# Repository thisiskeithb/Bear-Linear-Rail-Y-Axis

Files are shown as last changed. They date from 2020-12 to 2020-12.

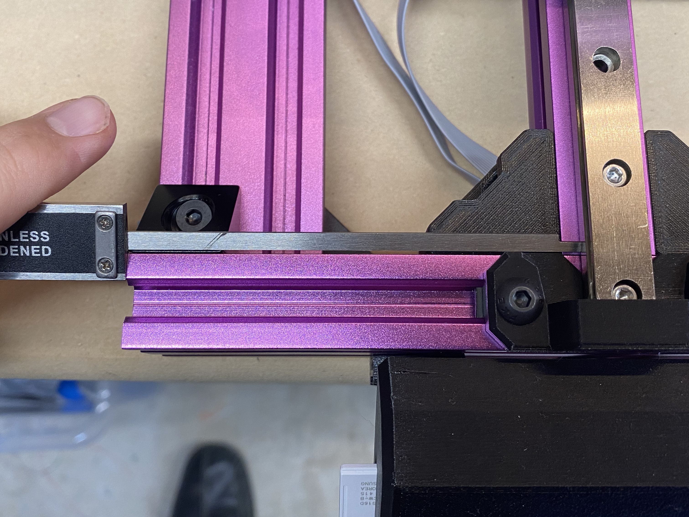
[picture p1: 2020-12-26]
img/left_rail_distance_2.jpg

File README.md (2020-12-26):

# Prusa MK3S Bear Y-Axis Linear Rail Upgrade

<p align="center">
  
</p>

## This guide is a work in progress
It is incomplete and subject to change. Use at your own risk.

## ⚠️ CAUTION! ⚠️

Before you begin, make sure you are using [MK3S Bear Upgrade V2.0](https://github.com/gregsaun/prusa_i3_bear_upgrade) or newer because the Y-axis uses the belt holder under the carriage to bump into the Y-axis motor holder. Without this upgrade, it will not pass Prusa's Self Test.

If you're using the [SKR Bear firmware](https://github.com/codiac2600/SKR-Bear-Marlin) this won't be an issue.

## Bill of Materials

| QTY | Length | Description | Source |
| :-: | :----: | :--- | :--- |
| 2 | 370mm  | MGN12 linear rail **\*** | |
| 3 | | MGN12H carriage block **\*** | |
| 2 | 331mm  | 2020 V-slot extrusion | |
| 18  | 8mm | M3 button head or cap head screw | [Amazon](https://amzn.com/B07B8FBT46/) / [OpenBuilds](https://openbuildspartstore.com/button-head-screws-m3-25-pack/) / [McMaster-Carr](https://www.mcmaster.com/91239A113) / [AliExpress](https://www.aliexpress.com/item/4000038065691.html) |
| 6 | 6mm | M3 flat head screw | [McMaster-Carr](https://www.mcmaster.com/91294A126) / [AliExpress](https://www.aliexpress.com/item/33049019185.html) |
| 18  | | M3 t-nuts | [Amazon](https://amzn.com/B07SDFCTD4/) / [OpenBuilds](https://openbuildspartstore.com/tee-nuts-m3-10-pack/) / [AliExpress](https://www.aliexpress.com/item/32825357262.html) |
| 20  | 8mm | M5 screws | [Amazon](https://amzn.com/B07B2RV4K6/) / [OpenBuilds](https://openbuildspartstore.com/low-profile-screws-m5-10-pack/) / [McMaster-Carr](https://www.mcmaster.com/91239A222) / [AliExpress](https://www.aliexpress.com/item/4000038065691.html) |
| 20  | | M5 t-nuts | [Amazon](https://amzn.com/B01HKMF2EE/) / [OpenBuilds](https://openbuildspartstore.com/tee-nuts-m5-10-pack/) / [AliExpress](https://www.aliexpress.com/item/32965780205.html) |

**\*** _If you are located in the USA, 2x 370mm MGN12 linear rails with dual carriage blocks from [Printed Solid](https://www.printedsolid.com/products/ldo-linear-rail-mgn12h-with-one-carriage-in-300-400-500-700mm-lengths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) will work. You will have one spare carriage block._

### Optional Bill of Materials
| QTY | Description | Source |
| :-: | :--- | :--- |
| 6 | 2028 aluminum corner bracket | [Amazon](https://amzn.com/B07B8FBT46/) / [AliExpress](https://www.aliexpress.com/item/4000767697780.html) |

## Printed Parts

Print all the parts below:

| QTY | Description |
| :-: | :--- |
| 3 | [Bearing Spacer](stl/bearing-spacer.stl) |
| 4 | [Rail Guard](stl/front-rail-guard-1-2.stl) |
| 2 | [MGN12 Linear Rail Alignment Tool](stl/linear_rail_alignment_tool-v1.stl) |
| 1 | [2020 Extrusion Build Helper](stl/build_helper_y-mgn12-mod-v3.stl) |
| 6 | [Corner Bracket](stl/corner-bracket-1.0-vv.stl) **\*\*** |

**\*\*** _Not needed if you purchased 6x 2028 aluminum corner brackets._

### Recommended Print Settings

- Filament material: PETG/ABS/ASA/PC/Nylon (Not PLA)
- Infill: 30% Gyroid
- Resolution: 0.2mm
- Supports: No
- Raft: No

## Assembly Guide

### This guide is a work in progress
It is incomplete and subject to change. Use at your own risk.

### Step 1 - Prepare Printer

Remove your bed, Y carriage, 8mm rods & bearings, and front & rear Y rod holders. You will only reuse your bed & Y carriage for this mod.

### Step TK - Prepare linear rails

Install 2x MGN12H carriage blocks on one MGN rail and 1x MGN12H carriage block on the second linear rail.

### Step TK - Mount linear rails to 2020 Extrusion

Attach linear rails to each 331mm 2020 V-slot extrusion using 9x M3x8 screws and M3 t-nuts. Use 2x printed [MGN12 Linear Rail Alignment Tools](stl/linear_rail_alignment_tool-v1.stl) to help align the linear rails on the 2020 extrusion.

### Step TK - Mount 2020 Extrusion to Bear Frame

Mount assembled linear rail and extrusion to the Bear frame using 6x M5x8 screws, 6x M5 t-nuts, and 6x printed [Corner Brackets](stl/corner-bracket-1.0-vv.stl) with 2x brackets in the front and 1x in the back, opposite of the Y-axis motor.

Ensure the linear rail with 2x MGN12H carriage blocks are on the left.

Leave the rightmost extrusion and rail loose for adjustment later.

Loosen all M5 screws on the leftmost linear rail.

### Step TK

Use [2020 Extrusion Build Helper](stl/build_helper_y-mgn12-mod.stl) to align the left 2020 extrusion/linear rail assembly 50mm to the right of the frame, front and back. Tighten the M5 screws making sure the 2020 extrusion stays aligned.

Install the four printed [Rail Guards](stl/front-rail-guard-1-2.stl) with 8x M5x8 screws & 8x M5 t-nuts to prevent the bed from sliding off the rails. Do not fully tighten M5 screws.

### Step TK

Attach printed [Bearing Spacers](stl/bearing-spacer.stl) to each bearing block with the small end oriented toward the back.

### Step TK

Attach the printed [Bearing Spacers](stl/bearing-spacer.stl) to each MGN12 carriage using 6x M3-6 flathead screws.

Attach the Y carriage to the printed [Bearing Spacers](stl/bearing-spacer.stl) using 6x M3-8 screws. Shift the rightmost rail and extrusion so it lines up without binding.

### Step TK

Tighten the 2020 V-slot extrusion to the frame.

### Step TK

Loosen all screws on rightmost linear rail.

### Step TK

Move the carriage as far forward as possible and tighten the most forward screw on the rail to the extrusion.

### Step TK

Slide the carriage as far back it would go and tighten the back most M3 8mm screw.

### Step TK

Tighten all M3 & M5 screws.

### Step TK

Reinstall bed.

_Repeat Steps TK-TK if your bed isn't sliding smoothly._

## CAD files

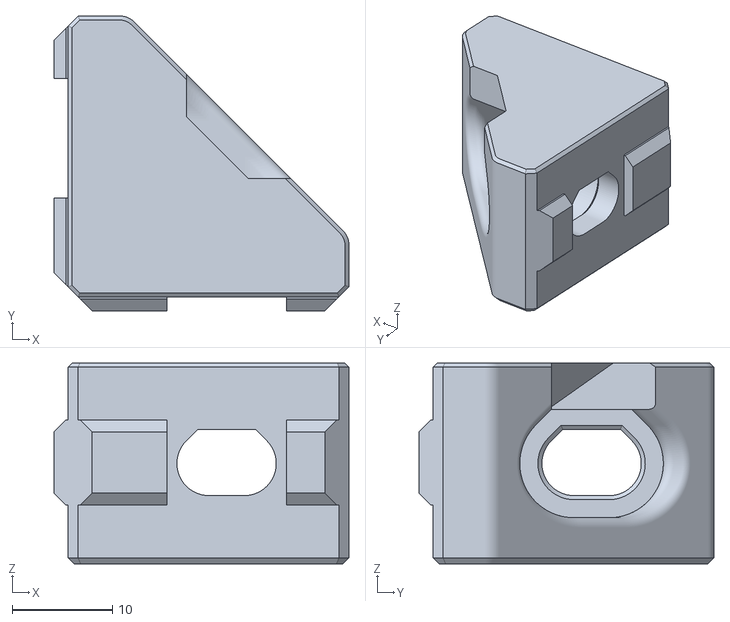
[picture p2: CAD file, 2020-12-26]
stl/corner-bracket-1.0-vv.stl
29.4 x 29.4 x 20.0

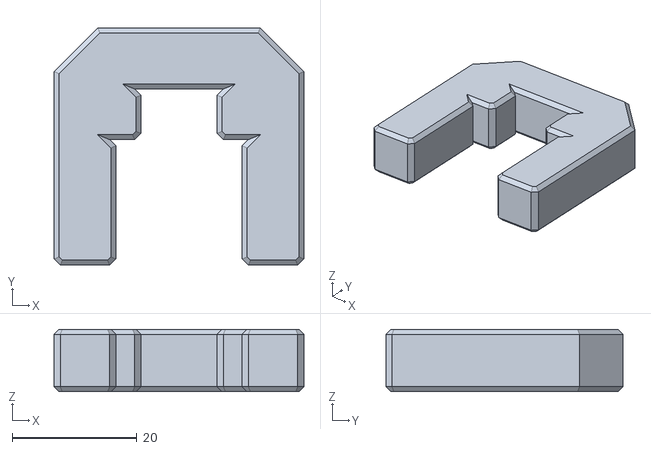
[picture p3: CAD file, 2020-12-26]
stl/linear_rail_alignment_tool-v1.stl
40.0 x 38.0 x 10.0

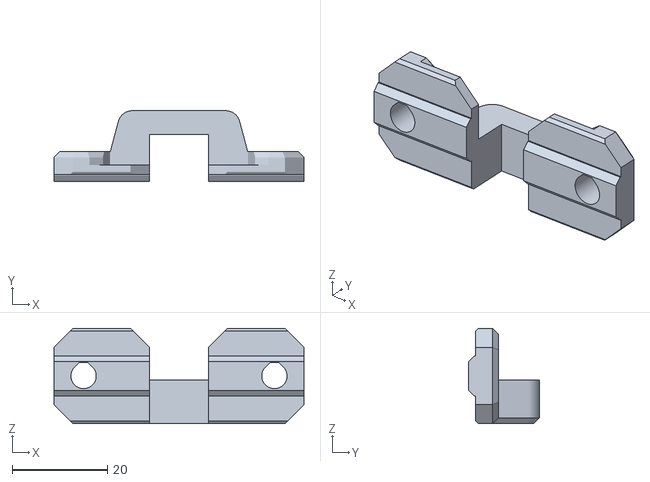
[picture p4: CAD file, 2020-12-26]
stl/rail-guard-1-2.stl
52.4 x 14.8 x 20.0

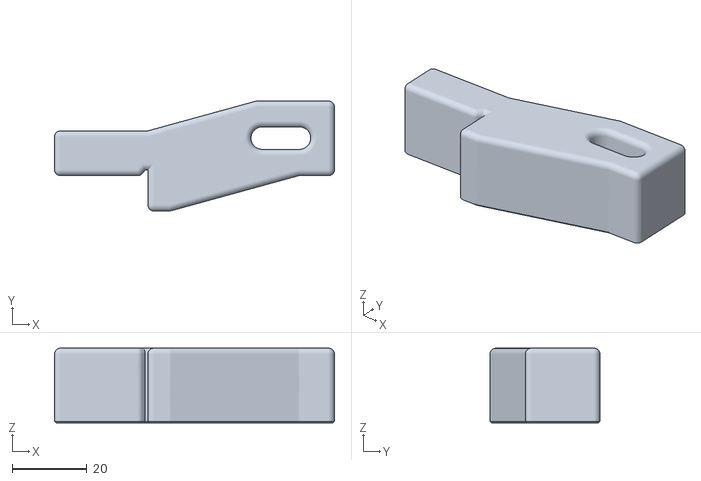
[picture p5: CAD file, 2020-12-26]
stl/build_helper_y-mgn12-mod-v3.stl
75.0 x 29.5 x 20.0

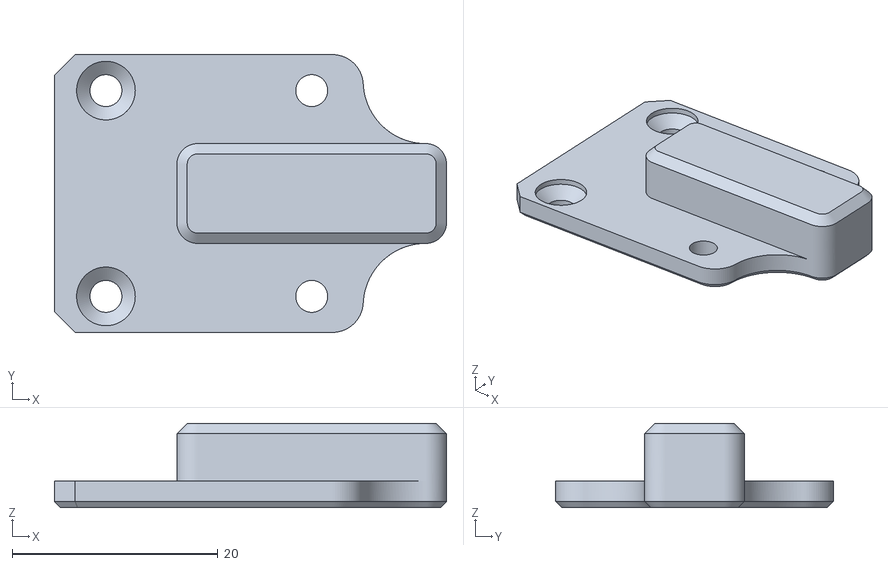
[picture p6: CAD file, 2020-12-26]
stl/bearing-spacer.stl
38.1 x 27.0 x 8.20
